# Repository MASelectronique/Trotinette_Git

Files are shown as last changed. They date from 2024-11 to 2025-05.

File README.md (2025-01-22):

Repos pour le système d'affichage de la trottinette électrique, projet étudiant du Cégep de Sherbrooke.

Code: Contient le code pour le prototype du système d'affichage.
Schéma: Contient les schémas (bloc, électrique et PCB) du prototype et du projet final.
Documentation: Contient les fichiers pour OSEntreprendre.

Créateurs: -Marc-Antoine Sauvé
           -Lucas Lalumière Longpré

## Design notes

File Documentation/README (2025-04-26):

Dossier Osentreprendre
Contient : 	- Osentreprendre v.2
			- PowerPoint du projet
 
Dossier PCB
Contient :	- Logo utilisé sur les PCB
			- Plan de test des PCB

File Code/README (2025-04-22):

Dossier principale (Code)

Contient : 	Fichier Controleur_client : Contient le code pour envoyer le JSON à partir du PCB de contrôle
		Fichier Developpement : Contient tous les anciens code utilisé l'ors du développement du projet
		Fichier EEZ_Studio : contient le projet du GUI de l'affichage
		Fichier Interface_V.1 : Projet à jour de l'affichage avec les librairies et le fichier main
		Fichier Interface_V.2 : Projet à jour de l'affichage et développement de l'intégration du JSON 
		Fichier Template_startip : C'Est un template pour partir un projet de zéro avec les lignes nécessaire pour que EEZ Studio, TFT, l'écran ainsi que le touch fonctionne			 
Language: C++
Environnement: Arduino avec board manager de ESP32 par Espressif Systems 2.0.14 (une version supérieur ne fonctionnera pas)
Plateforme: Arduino IDE 2.3.6

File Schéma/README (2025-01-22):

Dossier contenant le schéma pour le prototype et la version finale du système d'affichage.
Contient les schémas bloc, schémas électriques et PCB.

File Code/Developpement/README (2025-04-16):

Dossier secondaire (Developpement)

Contient : 	Fichier Accelerometre = Code pour le prototype du système d'affichage
		Fichier Affichage_retour_en_arriere (Plus utilisé) = Projet non commenté de test
		Fichier Affichage_test (Plus utilisé) = Développement du système d'affichage
		Fichier Affichage_touch_ui : Un test unitaire testant l'affichage, le touch de l'écran et le UI généré par EEZ studio. Inclus aussi toutes les libraires
		Fichier Telemetrie : Code de développement du module de télémétrie
		Fichier Touch_calibration = Code pour générer les données nécessaire à la calibration de l'écran
			
Language: C++
Environnement: Arduino avec board manager de ESP32 par Espressif Systems 2.0.14 (une version supérieur ne fonctionnera pas)
Plateforme: Arduino IDE 2.3.6

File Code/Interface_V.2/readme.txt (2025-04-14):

Dossier secondaire(Interface_V.2)

Contient : 	Fichier Affichage_V.2 : main pour faire afficher à l'écran avec des valeur aléatoire (en train d'intégrer le décodage du JSON)
		Fichier Libraries_backup : contient toute les libraries à jour pour faire fonctionner le projet

Language: C++
Environnement: Arduino avec board manager de ESP32 par Espressif Systems 2.0.14 (une version supérieur ne fonctionnera pas)
Plateforme: Arduino IDE 2.3.6

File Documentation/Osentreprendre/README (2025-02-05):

Dossier contenant tous les fichiers pour le concours OSEntreprendre.
Contient : 	- Texte explicatif
		- PowerPoint du projet
		- PowerPoint du présentoire

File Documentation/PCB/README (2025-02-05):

Dossier PCB
Contient :	- Logo utilisé sur les PCB
		- Plan de test des PCB

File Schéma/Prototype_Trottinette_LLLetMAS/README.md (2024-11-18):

Schéma électrique du prototype de l'affichage.
Concepteur: Lucas Lalumière Longpré

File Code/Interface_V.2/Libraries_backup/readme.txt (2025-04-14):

Dossier secondaire(Libraries_backup)

Contient : 		Fichier ArduinoJson : Librarie permettant le décodage d'un JSON 
			Fichier EspSoftwareSerial : Librarie permettant d'avoir un moniteur série en utilisant des GPIO différents de ceux proposé par l'ESP32
			Fichier ICM42670P : Librairie permettant la communication avec l'accéléromètre
			Fichier LVGL: Librarie avec la bonne configuration
			Fichier TFT_eSPI: Librarie avec la bonne configuration
			Fichier ui : interface généré de eez studio
			Fichier lv_conf.h : configuration de la livrairies de LVGL

Language: C++
Environnement: Arduino avec board manager de ESP32 par Espressif Systems 2.0.14 (une version supérieur ne fonctionnera pas)
Plateforme: Arduino IDE 2.3.6

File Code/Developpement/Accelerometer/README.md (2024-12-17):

Créateurs: 
  -Lucas Lalumière Longpré
  -Marc-Antoine Sauvé
Code pour le prototype du système d'affichage utilisé dans le projet de trottinette électrique. 
Calcule le roulis et le tangage d'un accéléromètre et l'affiche à un écran tactile. On peux aussi
tester la fonctionnalité tactile de l'écran. La DEL du MCU s'allume lorsque le roulis ou le tangage
est à plus de 30 degré (Trottinette sur le côté).

Librairies à installer:
  -TFT_eSPI (https://github.com/Bodmer/TFT_eSPI)

Plateforme: Platformio
Framework: Arduino
Langue: C++
Matériel:
  -MCU: ESP32-C3 DevkitC-02
  -Accel: MPU-6050
  -Écran: ILI9341

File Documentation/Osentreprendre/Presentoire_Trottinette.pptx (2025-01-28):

## Tableau de bord d'une trottinette électrique

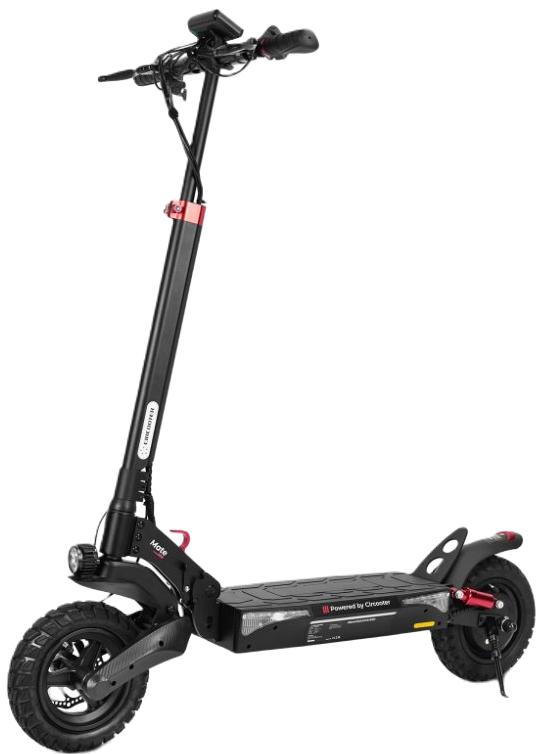
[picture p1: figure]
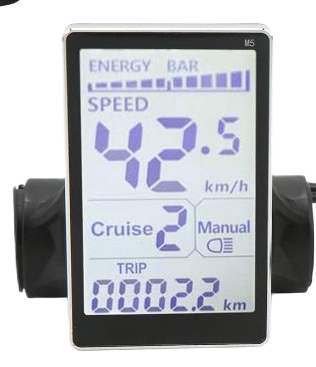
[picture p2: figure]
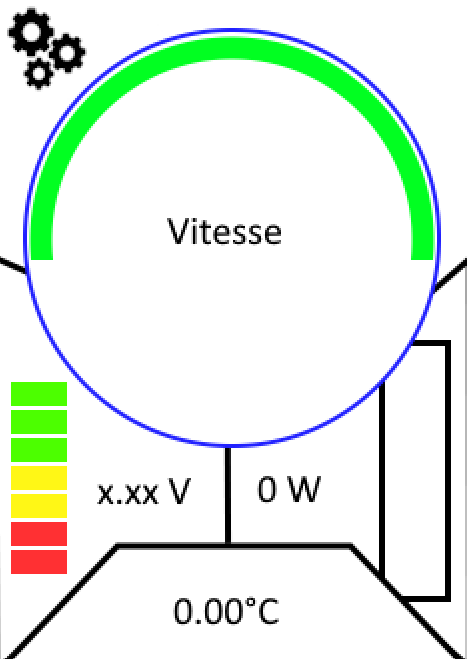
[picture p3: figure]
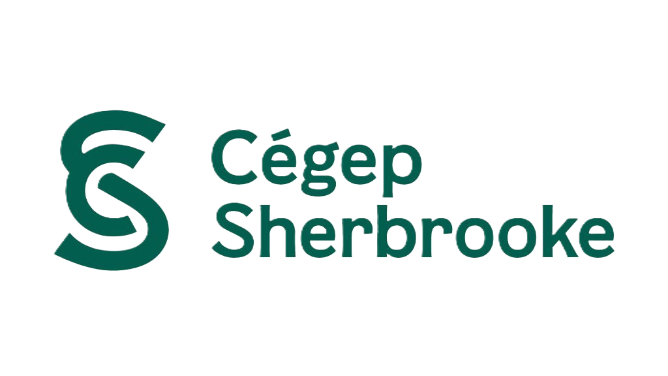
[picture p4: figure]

Tableau de bord

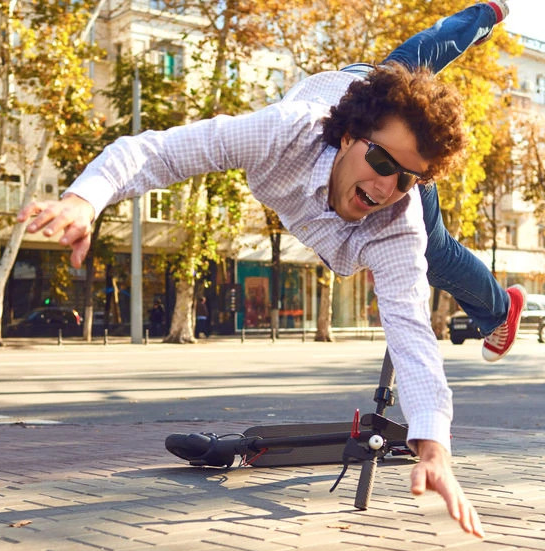
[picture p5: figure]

Détection de chute

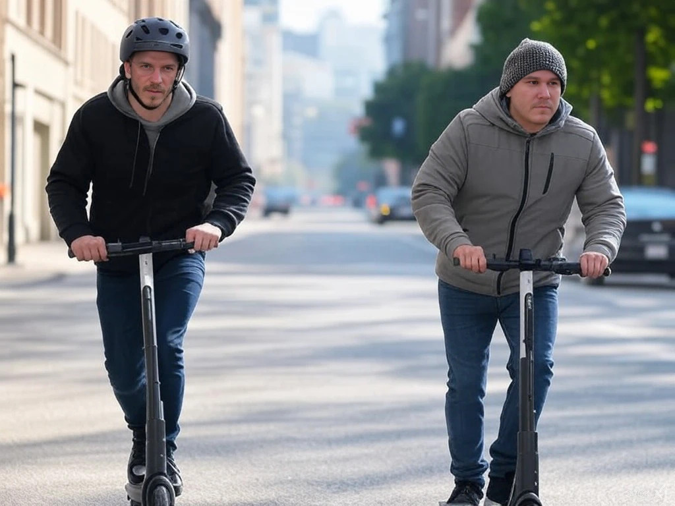
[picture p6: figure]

Marc-Antoine Sauvé et
Lucas Lalumière Longpré

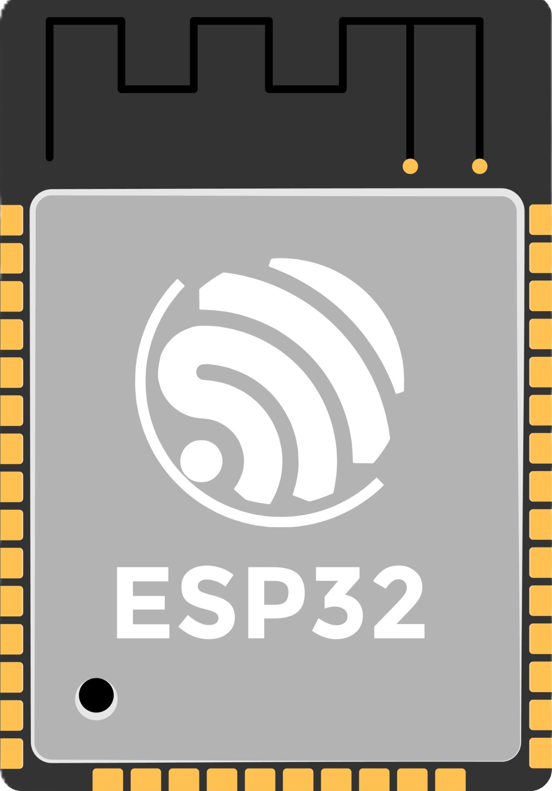
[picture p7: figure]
Vittascience — ESP32

Microcontrôleur

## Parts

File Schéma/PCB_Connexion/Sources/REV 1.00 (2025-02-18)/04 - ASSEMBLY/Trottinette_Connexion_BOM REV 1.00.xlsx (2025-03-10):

Bill of Material
Board | Trotinette_Connexion |  | Concepteur Principal |  | Marc-Antoine Sauvé |  |  | 1
Cours | 247-67P-SH PROJET DE FIN D'ÉTUDES |  | Date du projet |  | 22 janvier 2025 |  |  | 00
Département | Technologies du génie électrique |  | Date de génération du BOM |  | 2025-02-18
Révision | 1.00 |  | Heure de génération du BOM |  | 10:06
Nombre de PCB | 1 |  | Variant |  | None
Item Number | Designator | Layer | Description | Comment | Package / Case | Supplier 1 | Supplier Part Number 1 | Quantity | Quantity Total | Note
 | C1 | Top | General Purpose Ceramic Capacitor, 0603, 100nF, 20%, X7R, 15%, 10V | 0603ZC104MAT2A |  |  |  | 1 | 1
 | C2, C4 | Top | CAP CER 10UF 10V X5R 0603 | 10 µF | 0603 (1608 Metric) | DigiKey | 490-12311-1-ND | 2 | 2
 | C3, C5 | Top | CAP ALUM 100UF 20% 10V SMD | 100 µF | Radial, Can - SMD | DigiKey | 1189-2392-1-ND | 2 | 2
 | J1 | Bottom |  | 685119136923 |  |  |  | 1 | 1
 | Q1 | Bottom | MOSFET P-CHA 60V 720MW SOT23 | DMP6350S-7 |  |  |  | 1 | 1
 | R1 | Top | RESA-AS 0603 0R JUMPER 100MW | 0 Ohms | 0603 (1608 Metric) | DigiKey | CR0603AJ/-000EASCT-ND | 1 | 1
 | R2 | Bottom | 30Ohms | ERJ3EKF30R0V |  |  |  | 1 | 1
 | R3 | Top | RES 180 OHM 1% 1/8W 0603 | 180 Ohms | 0603 (1608 Metric) | DigiKey | RNCP0603FTD180RCT-ND | 1 | 1
 | R4 | Top | RES SMD 300 OHM 1% 1/10W 0603 | 300 Ohms | 0603 (1608 Metric) | DigiKey | 541-300HCT-ND | 1 | 1
 | R5 | Bottom | RES 10K OHM 0.1% 1/16W 0603 | 10 kOhms | 0603 (1608 Metric) | DigiKey | RNCS0603BKE10K0CT-ND | 1 | 1
 | S1 | Top | 3.2" 240x320 TFT LCD ILI9341 | ILI9341 |  |  |  | 1 | 1
 | U1 | Top | 800mA Low-Dropout Linear Regulator, 4-pin SOT-223 | LM1117MPX-ADJ |  |  |  | 1 | 1
Commentaires ou instruction spécialies

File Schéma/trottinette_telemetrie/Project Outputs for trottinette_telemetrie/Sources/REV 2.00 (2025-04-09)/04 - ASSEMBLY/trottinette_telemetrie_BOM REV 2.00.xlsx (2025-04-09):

Bill of Material
Board | Trottinette - Module de télémétrie |  | Concepteur Principal |  | Lucas Lalumière Longpré |  |  | 2
Cours | 247-67P-SH PROJET DE FIN D'ÉTUDES |  | Date du projet |  | 08-04-2025 |  |  | 00
Département | Technologies du génie électrique |  | Date de génération du BOM |  | 4/9/2025
Révision | 2.00 |  | Heure de génération du BOM |  | 9:57 AM
Nombre de PCB | 1 |  | Variant |  | None
Item Number | Designator | Layer | Description | Comment | Package / Case | Supplier 1 | Supplier Part Number 1 | Quantity | Quantity Total | Note
 | C1, C13 | Top | CAP ALUM 100UF 20% 10V SMD | 100 µF | Radial, Can - SMD | DigiKey | 1189-2392-1-ND | 2 | 2
 | C2, C3, C8, C9, C14 | Top, Bottom | CAP CER 10UF 10V X5R 0603 | 10 µF | 0603 (1608 Metric) | DigiKey | 490-12311-1-ND | 5 | 5
 | C4, C5, C10, C11 | Bottom, Top | General Purpose Ceramic Capacitor, 0603, 100nF, 20%, X7R, 15%, 10V | 0603ZC104MAT2A |  |  |  | 4 | 4
 | C6 | Top | CAP CER 0603 10NF 16V X7R 10% | 10000 pF | 603 | DigiKey | 399-17880-1-ND | 1 | 1
 | C7 | Top | CAP CER 2.2UF 16V Y5V 0603 | 2.2 µF | 603 | DigiKey | 311-3416-1-ND | 1 | 1
 | C12 | Top | CAP CER 10000PF 100V X7R 0603 | 10000 pF | 0603 (1608 Metric) | DigiKey | 311-3100-1-ND | 1 | 1
 | D1 | Top | TVS DIODE 5.25V 17V SOT666 | USBLC6-2P6 |  |  |  | 1 | 1
 | D2 | Top | DIODE SCHOTTKY 15V 1A DO214BA | LSM115JE3/TR13 |  |  |  | 1 | 1
 | D3 | Top | LED GREEN 0603 SMD | Green | 0603 (1608 Metric) | DigiKey | 350-4373-1-ND | 1 | 1
 | D4 | Top | LED YELLOW 0603 SMD | Yellow | 0603 (1608 Metric) | DigiKey | 350-4349-1-ND | 1 | 1
 | J1 | Top | CONN RCP USB2.0 TYP C 24P SMD RA | DX07S016JA1R1500 |  |  |  | 1 | 1
 | J2, MT1, R12, R14, R15, R16 | Top |  | 685119136923, ICM-42670-P, ERJ3EKF30R0V |  |  |  | 6 | 6
 | P1 | Bottom | WR-PHD Pin Header, THT, Vertical, pitch 2.54mm, 1 Row, 6P | 61300611121 |  |  |  | 1 | 1
 | P2 | Bottom | WR-PHD Pin Header, THT, Vertical, pitch 2.54mm, 1 Row, 8P | 61300811121 |  |  |  | 1 | 1
 | P3 | Top | WR-PHD Pin Header, THT, Vertical, pitch 2.54mm, 1 Row, 2P | 61300211121 |  |  |  | 1 | 1
 | R1 | Top | RES 150 OHM 1% 1/10W 0603 | 150 Ohms | 0603 (1608 Metric) | DigiKey | RMCF0603FT150RCT-ND | 1 | 1
 | R2 | Top | RES 250 OHM 5% 1/8W 0603 | 250 Ohms | 0603 (1608 Metric) | DigiKey | 716-1168-1-ND | 1 | 1
 | R3, R11 | Bottom | RES 5.1K OHM 1% 1/10W 0603 | 5.1 k | 603 | DigiKey | RMCF0603FT5K10CT-ND | 2 | 2
 | R4, R5, R6, R10 | Bottom, Top | RES 10K OHM 0.1% 1/16W 0603 | 10k | 0603 (1608 Metric) | DigiKey | RNCS0603BKE10K0CT-ND | 4 | 4
 | R7, R8 | Top | RES 124K OHM 1% 1/10W 0603 | 124 k | 0603 (1608 Metric) | DigiKey | RMCF0603FT124KCT-ND | 2 | 2
 | R9 | Bottom | RES 63.4K OHM 1% 1/10W 0603 | 63.4 k | 0603 (1608 Metric) | DigiKey | RMCF0603FT63K4CT-ND | 1 | 1
 | R13 | Top | 0603 26 AMP JUMPER | 0 Ohms | 0603 (1608 Metric) | DigiKey | JR0603X26ECT-ND | 1 | 1
 | R17, R18 | Top | RES SMD 1K OHM 0.1% 1/16W 0603 | 1 kOhms | 0603 (1608 Metric) | DigiKey | A119887CT-ND | 2 | 2
 | TP1 | Top | TPO - PC TEST POINT MINI - SMD | TPO_SMD_5019 |  |  |  | 1 | 1
 | U1 | Top | 800mA Low-Dropout Linear Regulator, 4-pin SOT-223 | LM1117MPX-ADJ |  |  |  | 1 | 1
 | U2 | Top | Bluetooth, WiFi 802.11b/g/n, Bluetooth v5.0 Transceiver Module 2.4GHz Antenna Not Included, U.FL Surface Mount | ESP32-S3-WROOM-1U-N16R8 |  |  |  | 1 | 1
 | U3 | Top | Low Quiescent Current, Programmable-Delay Supervisory Circuit, 1 Supply Monitored, -40 to 125 degC, 6-pin SOT-23 (DBV), Green (RoHS & no Sb/Br) | TPS3808G01DBVR |  |  |  | 1 | 1
Commentaires ou instruction spécialies

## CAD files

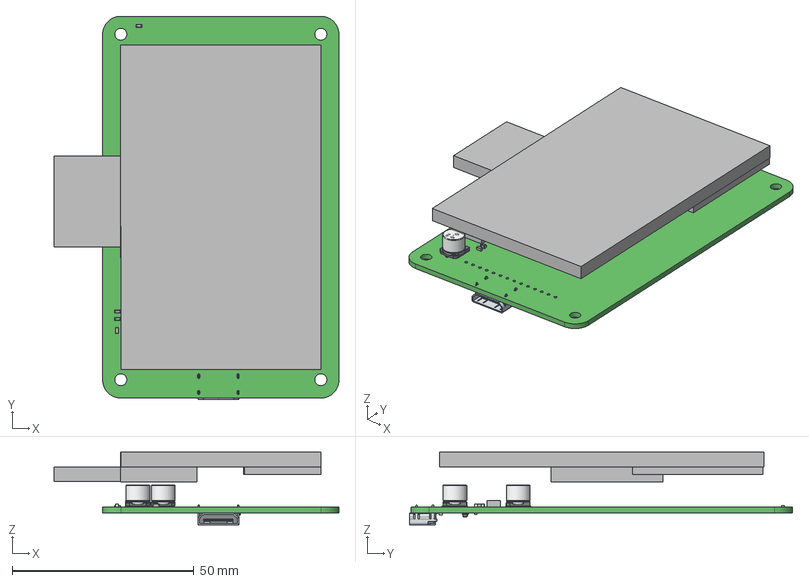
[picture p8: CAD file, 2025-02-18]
Schéma/PCB_Connexion/Sources/REV 1.00 (2025-02-18)/05 - 3D MODEL/Trottinette_Connexion_PCB REV 1.00.step
78.4 x 105.4 x 20.0 mm
Extruded x 8
0603 resistor x 4
pins
part number & logo
CAP ALSMD - 6.6 x 6.6 x 6.1 x 2
0603 cap x 2
Terminals
AVX
685119136923_Housing
685119136923_Shielding
685119136923_Housing2
685119136923_Pin1 x 18
685119136923_Pin2

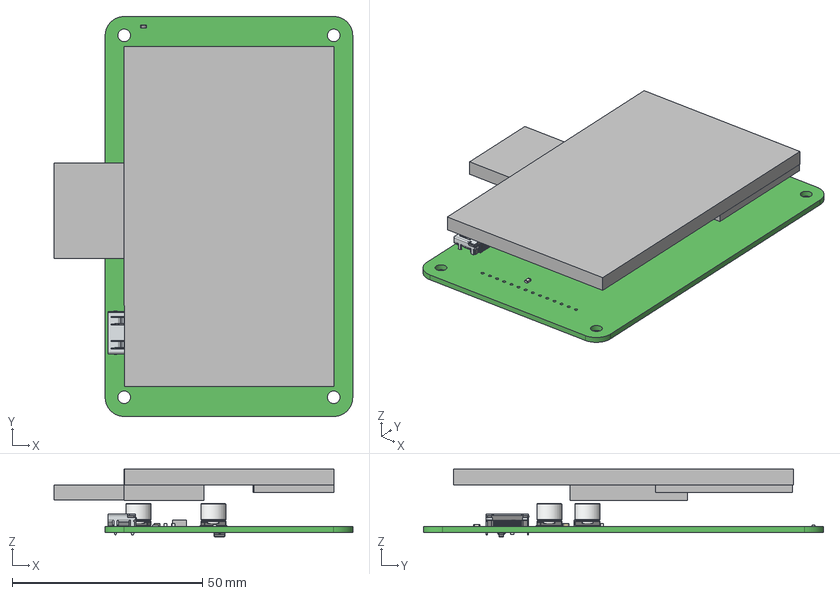
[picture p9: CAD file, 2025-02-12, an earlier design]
Schéma/PCB_Connexion/Sources/REV 1.00 (2025-02-11)/05 - 3D MODEL/Trottinette_Connexion_PCB REV 1.00.step
78.4 x 105.0 x 17.8 mm
0603 resistor x 4
pins
part number & logo
Extruded x 8
CAP ALSMD - 6.6 x 6.6 x 6.1 x 2
0603 cap x 2
Terminals
AVX
685119136923_Housing
685119136923_Shielding
685119136923_Housing2
685119136923_Pin1 x 18
685119136923_Pin2

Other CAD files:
Schéma/PCB_Connexion/Trottinette_Connexion_2L.step
Schéma/PCB_Connexion/Sources/REV 1.00 (2025-02-11)/05 - 3D MODEL/Trottinette_Connexion_PCB REV 1.00.x_t
Schéma/PCB_Connexion/Sources/REV 1.00 (2025-02-18)/05 - 3D MODEL/Trottinette_Connexion_PCB REV 1.00.x_t

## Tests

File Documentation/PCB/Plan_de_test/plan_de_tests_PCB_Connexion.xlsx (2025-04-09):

 | Plan de tests
Nom du PCB | Trottinette_Connexion | Préparé par | Marc-Antoine Sauvé
Cours | 247-67P-SH PROJET DE FIN D'ÉTUDES | Testeur | Lucas Lalumière Longpré
Département | Technologies du génie électrique | date | 27/2/2025
Révision | 1.00
Fonction | Test | Résultat | Commentaires
Régulateur | La tension d'entrée est à 5V | Réussi
 | La tension de sortie est à 3V3 | Réussi
Écran | Est-ce que la chip sur l'écran pour activé le touch est présente? | Réussi
 | Est-ce que l'écran s'insert bien dans les pin header femelle? | Réussi
 | Insérer l'écran sur le PCB de connexion, connecter le port mini-HDMI du PCB de connexion à celui du PCB de télémétrie. Brancher le port USB-C du PCB de télémétrie pour alimenter le tout. Mettre le programme <<Accelerometre>> du git dans le MCU à l'aide de plateforme.io. Est-ce que l'écran affiche les angles ?
 | En gardant le branchement mentionné plus haut ainsi que le code, est-ce que lorsqu'on touche l'écran, il est affiché à l'écran.
Alimentation | Il n'y a pas de court-circuit à l'alimentation | Réussi | 400 Ω entre GND et 3V3
Modifications / commentaires pour une deuxième version du PCB
1 | Cable HDMI ne s'insert pas comme il faut
2
3
4
5
6
7
8
9
10

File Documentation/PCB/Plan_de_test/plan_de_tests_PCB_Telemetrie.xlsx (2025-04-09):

 | Plan de tests
Nom du PCB | trottinette_telemetrie | Préparé par | Marc-Antoine Sauvé
Cours | Techniques de conception d'un prototype (247-425-SH) | Testeur
Département | Technologies du génie électrique | date
Révision | 1.00
Fonction | Test | Résultat | Commentaires
Pour cette section, brancher le PCB de télémétrie par USB-C, connecter le port mini-HDMI au PCB de connexion et programmer le MCU avec le programme du prototype (Git)
Regulateur 5V à 3V3 | La tension d'entrée est à 5V | Réussi | 4.79 V Mesuré
 | La tension de sortie est à 3V3 | Réussi | 3.32 V Mesuré
 | Le régulateur supporte un courant de sortie de 300mA (3.3V en sortie avec une resistance de 11ohm, 5Watt) | Réussi | 303 mA mesuré
Acceléromètre | Est ce qu'on peut lire les données de l'accélérateur | Réussi
I2C
Interruption | À l'aide d'un oscilloscope, est ce que les interruptions de l'accéléromètre deviennent active lorsque le PCB est sur le coter? | Réussi | Il y a un délai de 2 sec pour que l'angle soit détectée
Circuit de protection | Un court-circuit sur la sortie du régulateur ne court-circuite pas l'alimentation USB de 5V | Réussi
MOSFET / signal LED_Control | Est-ce qu'on peut fermer l'écran à l'aide du signal LED | Réussi
Pour cette section, déconnecter le cabe USB-C et le connecteur mini-HDMI.
Propriétés physique | Est-ce que les pin header s'insert facilement dans le PCB de contrôle de la trottinette? | Réussi
Redémarrage | Le bouton de reset du PCB de contrôle permet-il un bon redémarrage du MCU du PCB de télémétrie ? | Réussi
Court-circuit | Il n'y a pas de court-circuit entre 5V/VUSB et GND | Réussi | Environ 260 kΩ entre 5V et GND
Modifications / commentaires pour une deuxième version du PCB
1 | résistance de pull down sur GPIO46 pour boot mode
2 | DEL verte pour alimentation
3 | Déplacer CON_GPIO18 et CON_GPIO21 sur les pattes 10 et 11 du MCU
4 | Réduction de la longueur des traces USB
5 | Enlever la pull-up sur EN
6 | Changer pattes UART
7
8
9
10

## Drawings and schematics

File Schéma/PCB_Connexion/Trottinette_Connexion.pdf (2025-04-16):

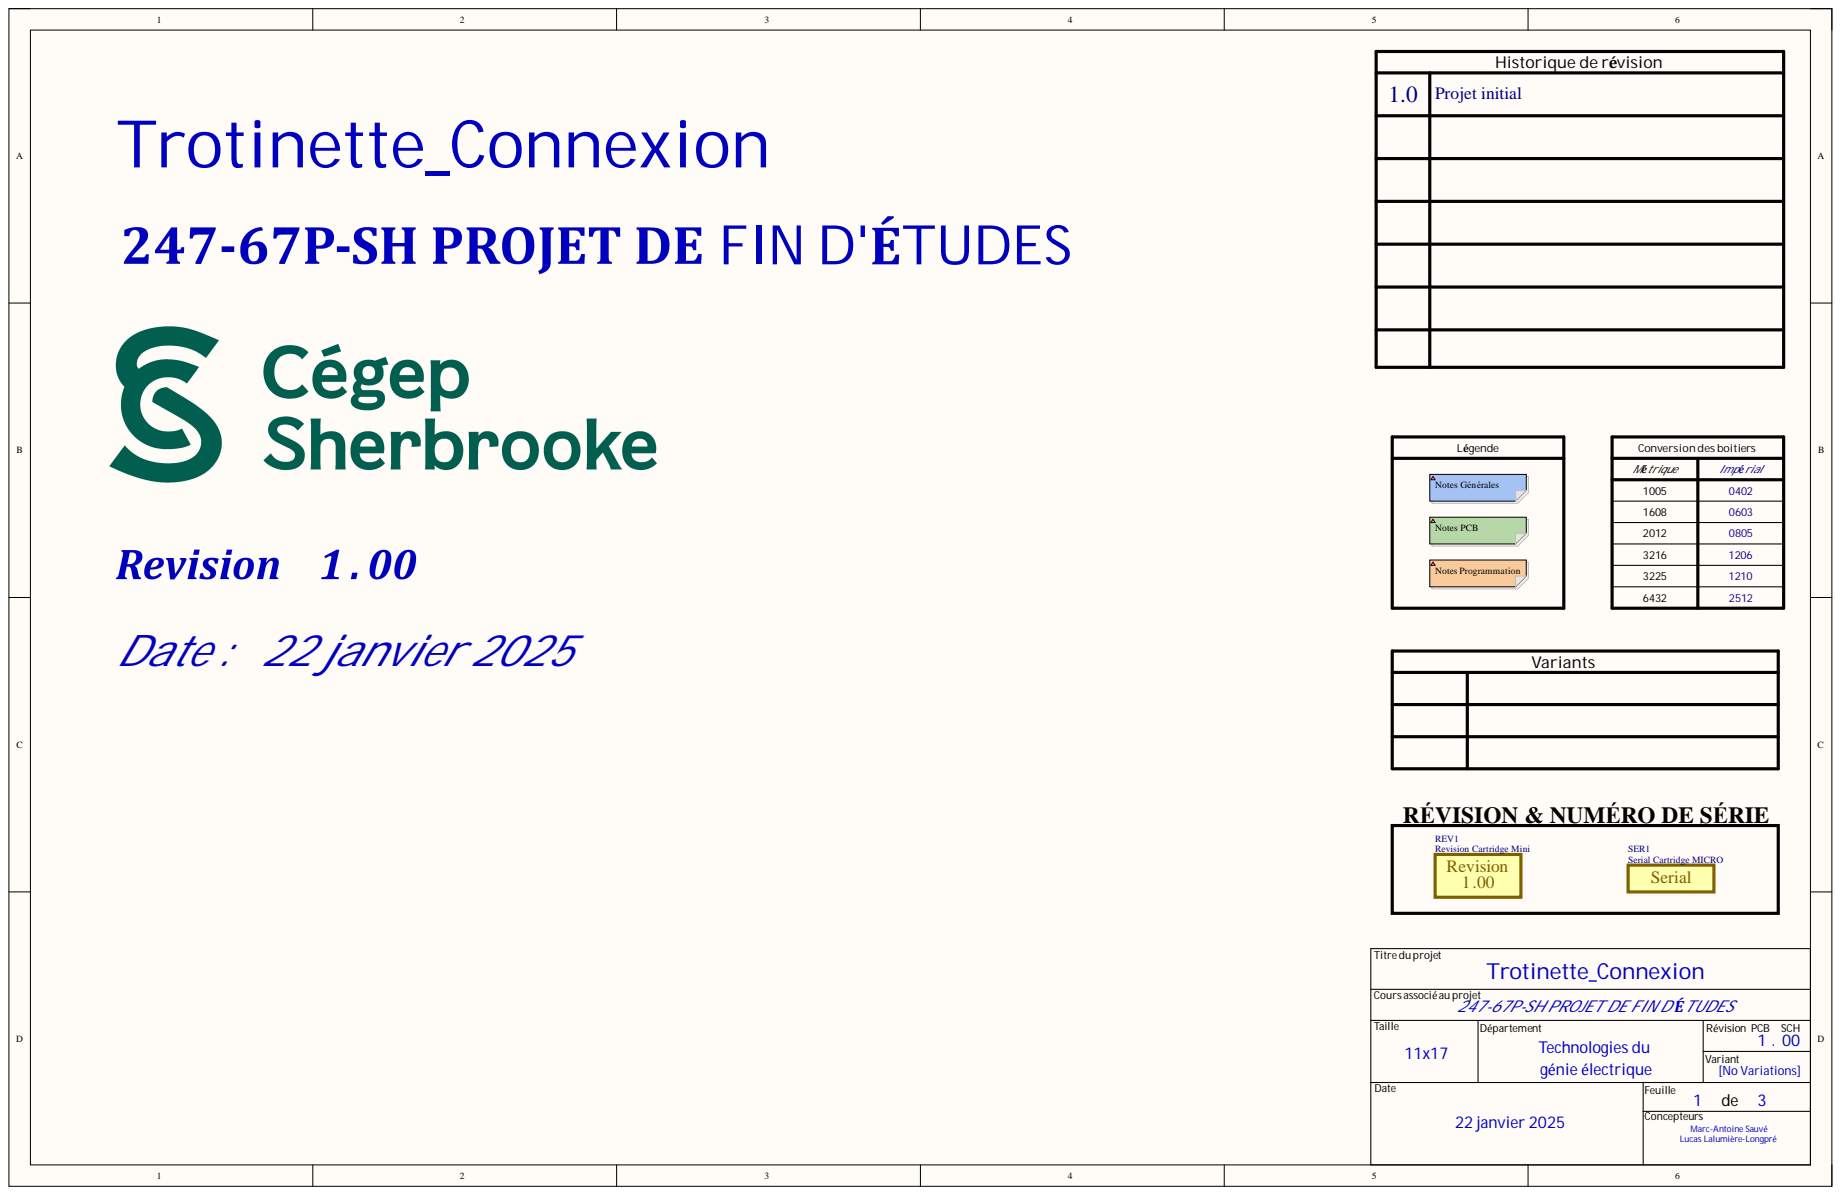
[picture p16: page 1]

-SH PROJET DE FIN D

Titr
rotinette_Connexion Cours associé au projet

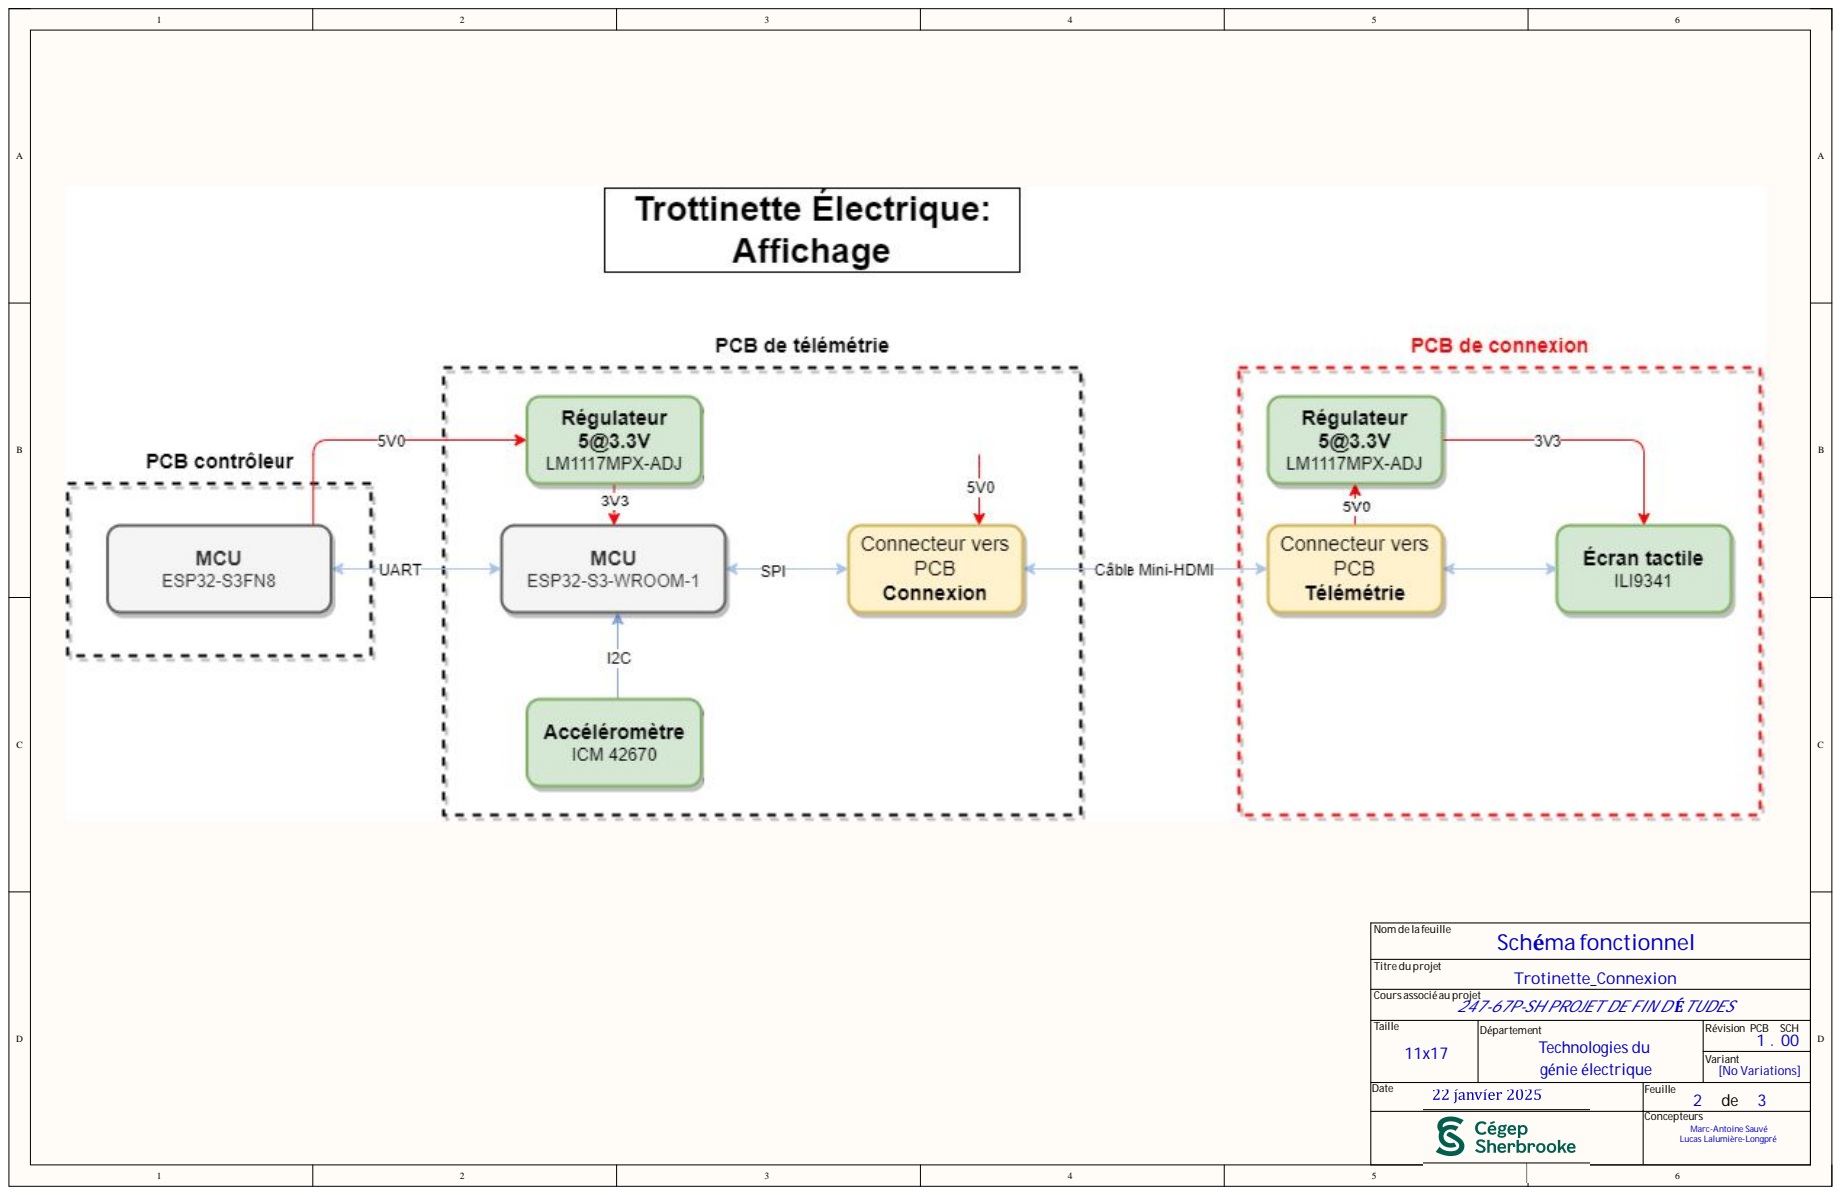
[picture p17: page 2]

Nom de la feuille

Titredu projet
Trotinette_Connexion Cours associé au projet

247-67P-SH PROJET DE FIN D'ÉTUDES

Date 22 janvier 2025 | Feuille 2 de Concepteurs 3

Marc-Antoine Sauvé Lucas Lalumière-Longpré

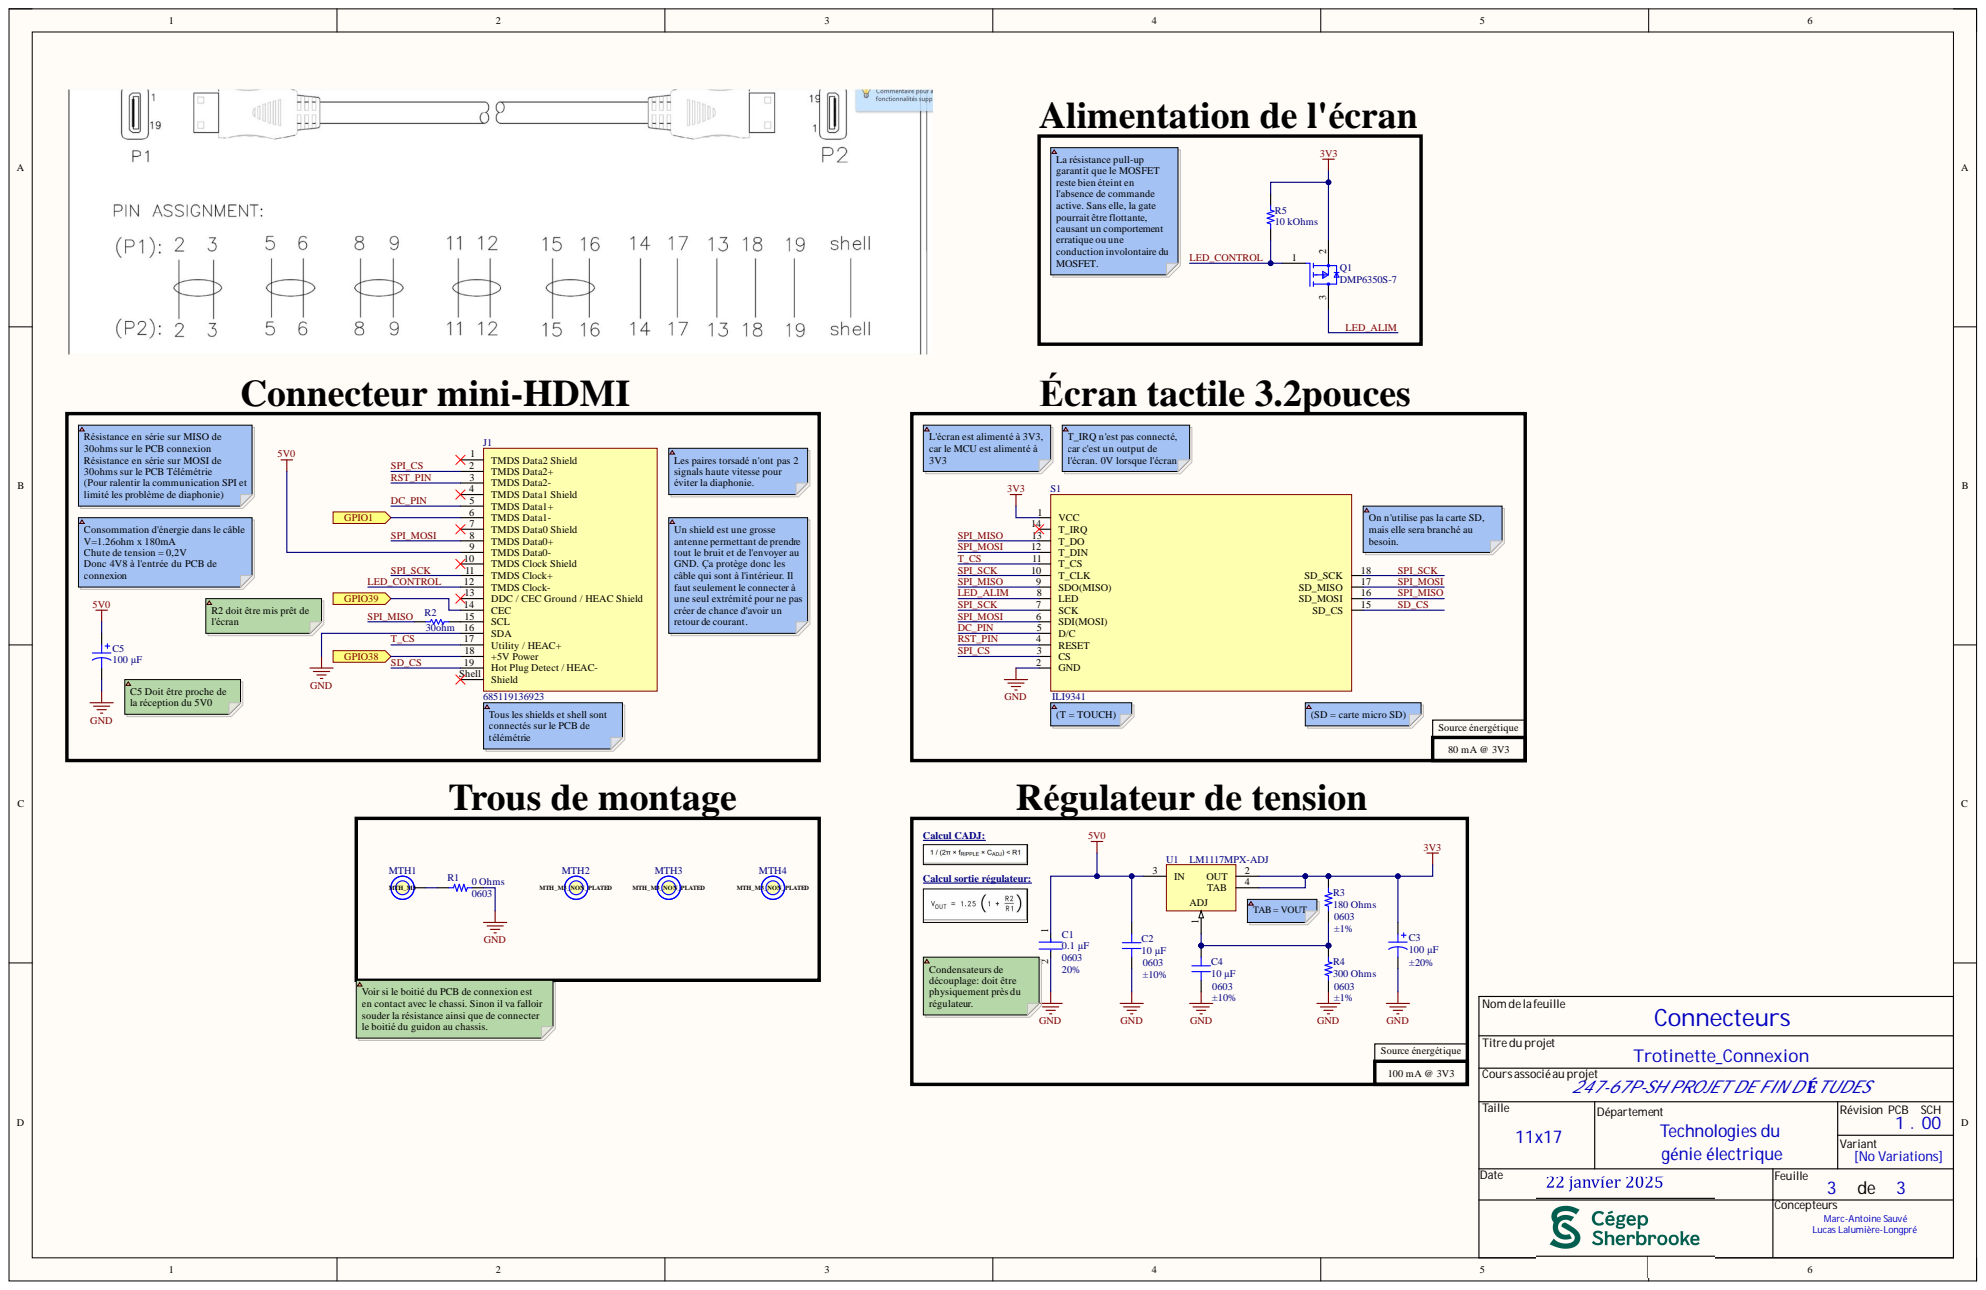
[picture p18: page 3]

Connecteur mini-HDMI Trous de montage

ésistance en
ms sur le PCB con
ms sur le PCB
tir la com

érie sur MISO de

mais elle sera branch
besoin

tilise pas la carte SD,

ten
t le bruit et de l'envoyer au
Ça prot
âble qui son
t seulemen
ne seul ext
retour de couran

ée du PCB de

éer de chance d'avoir

és sur le PCB de

Condensateurs de découplage: doit ê

Voir si le boit
en con
souder la
le boit

tact avec le chassi. Sinon il va falloir

é du PCB de con

ésistance ainsi que de con
é du guidon au chassis.

Date 22 janv ier 2025 | Feuil l e 3 de Concepteurs 3

Marc-A n toi n e Sa uv é Lu cas La l umi ère-Lon gp r é

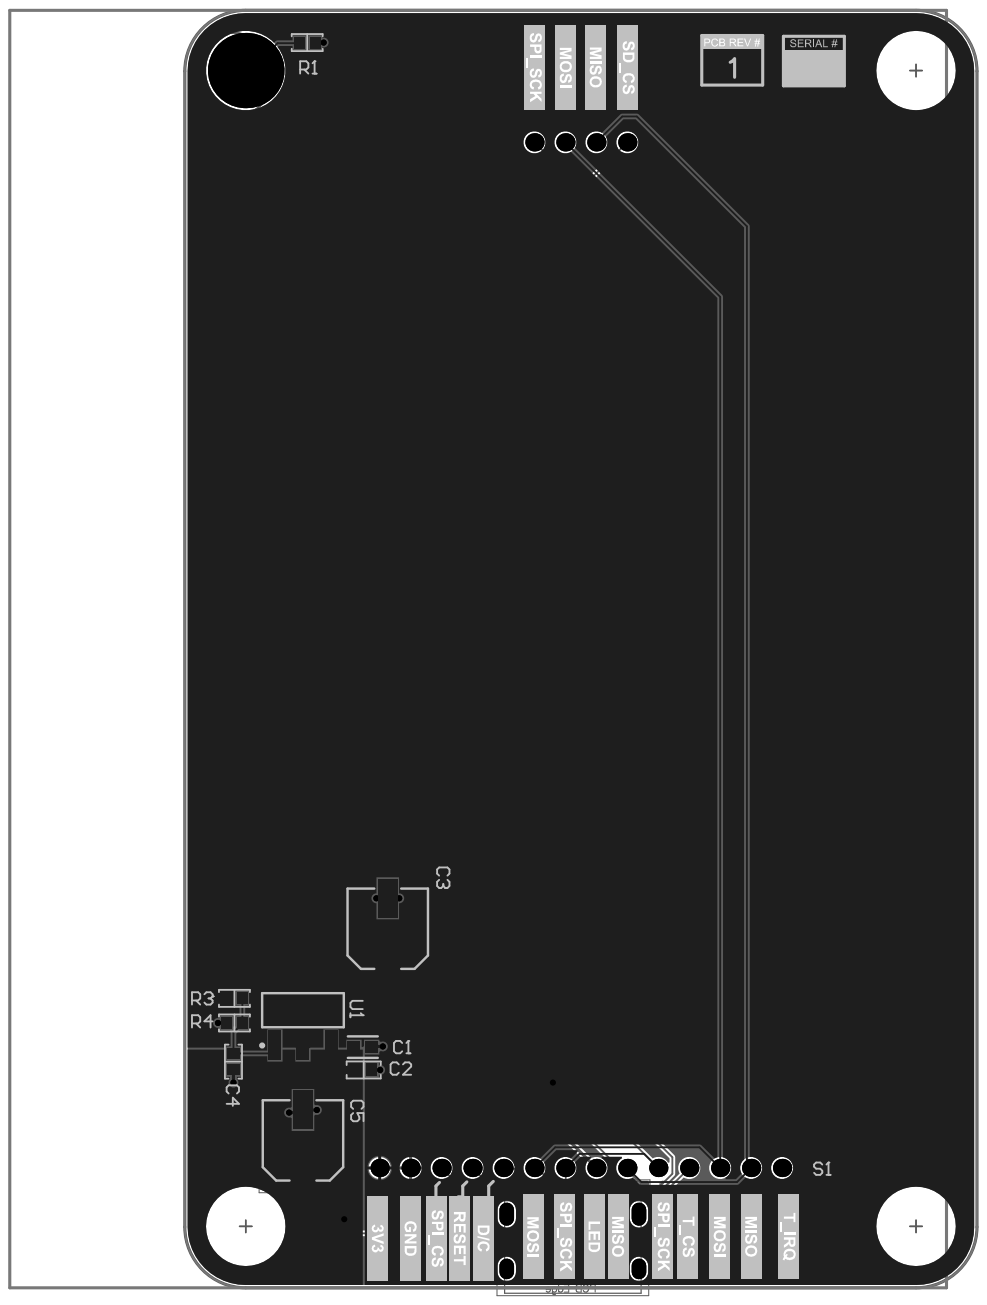
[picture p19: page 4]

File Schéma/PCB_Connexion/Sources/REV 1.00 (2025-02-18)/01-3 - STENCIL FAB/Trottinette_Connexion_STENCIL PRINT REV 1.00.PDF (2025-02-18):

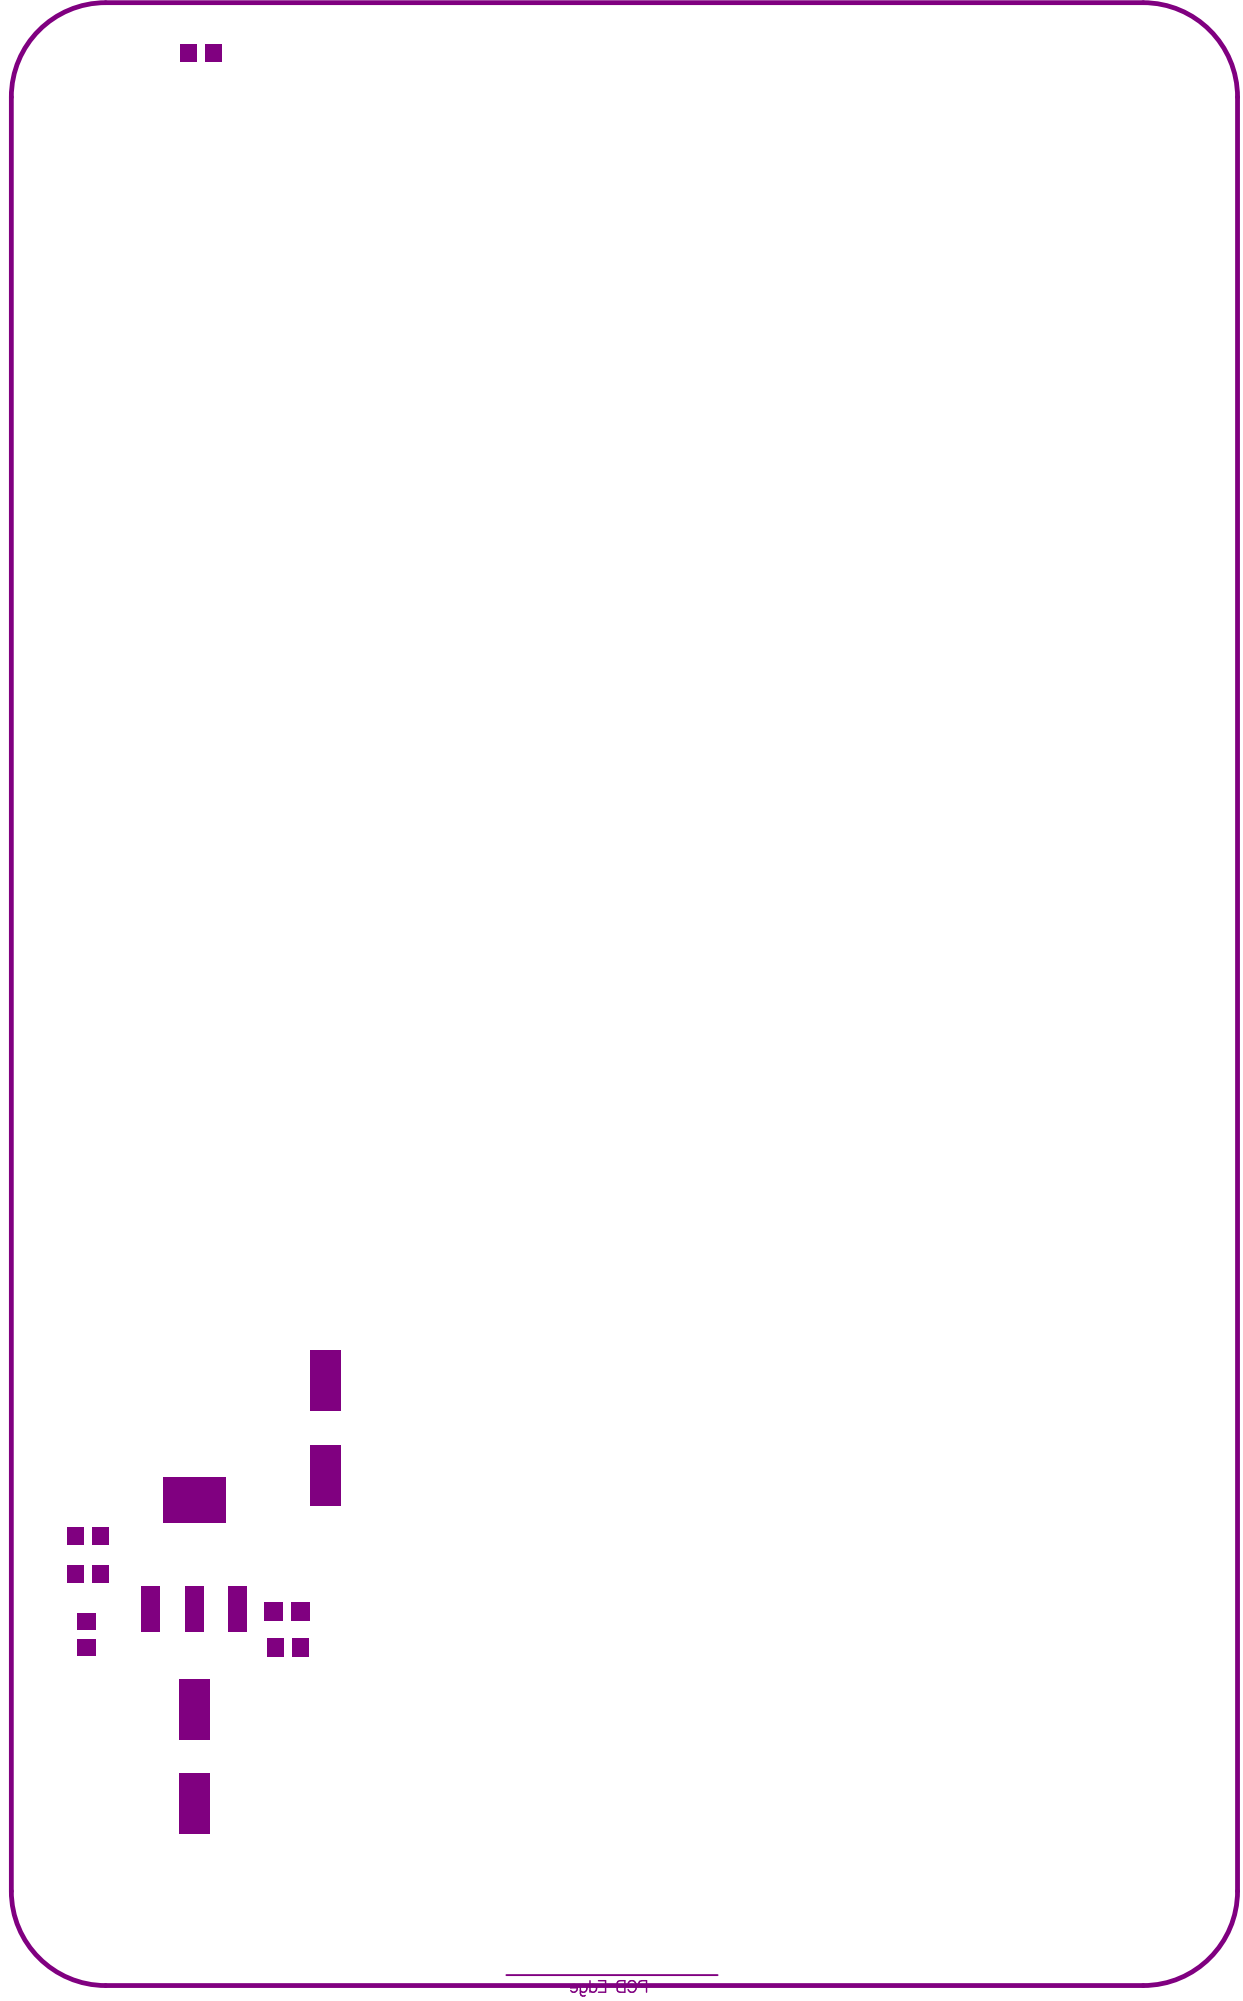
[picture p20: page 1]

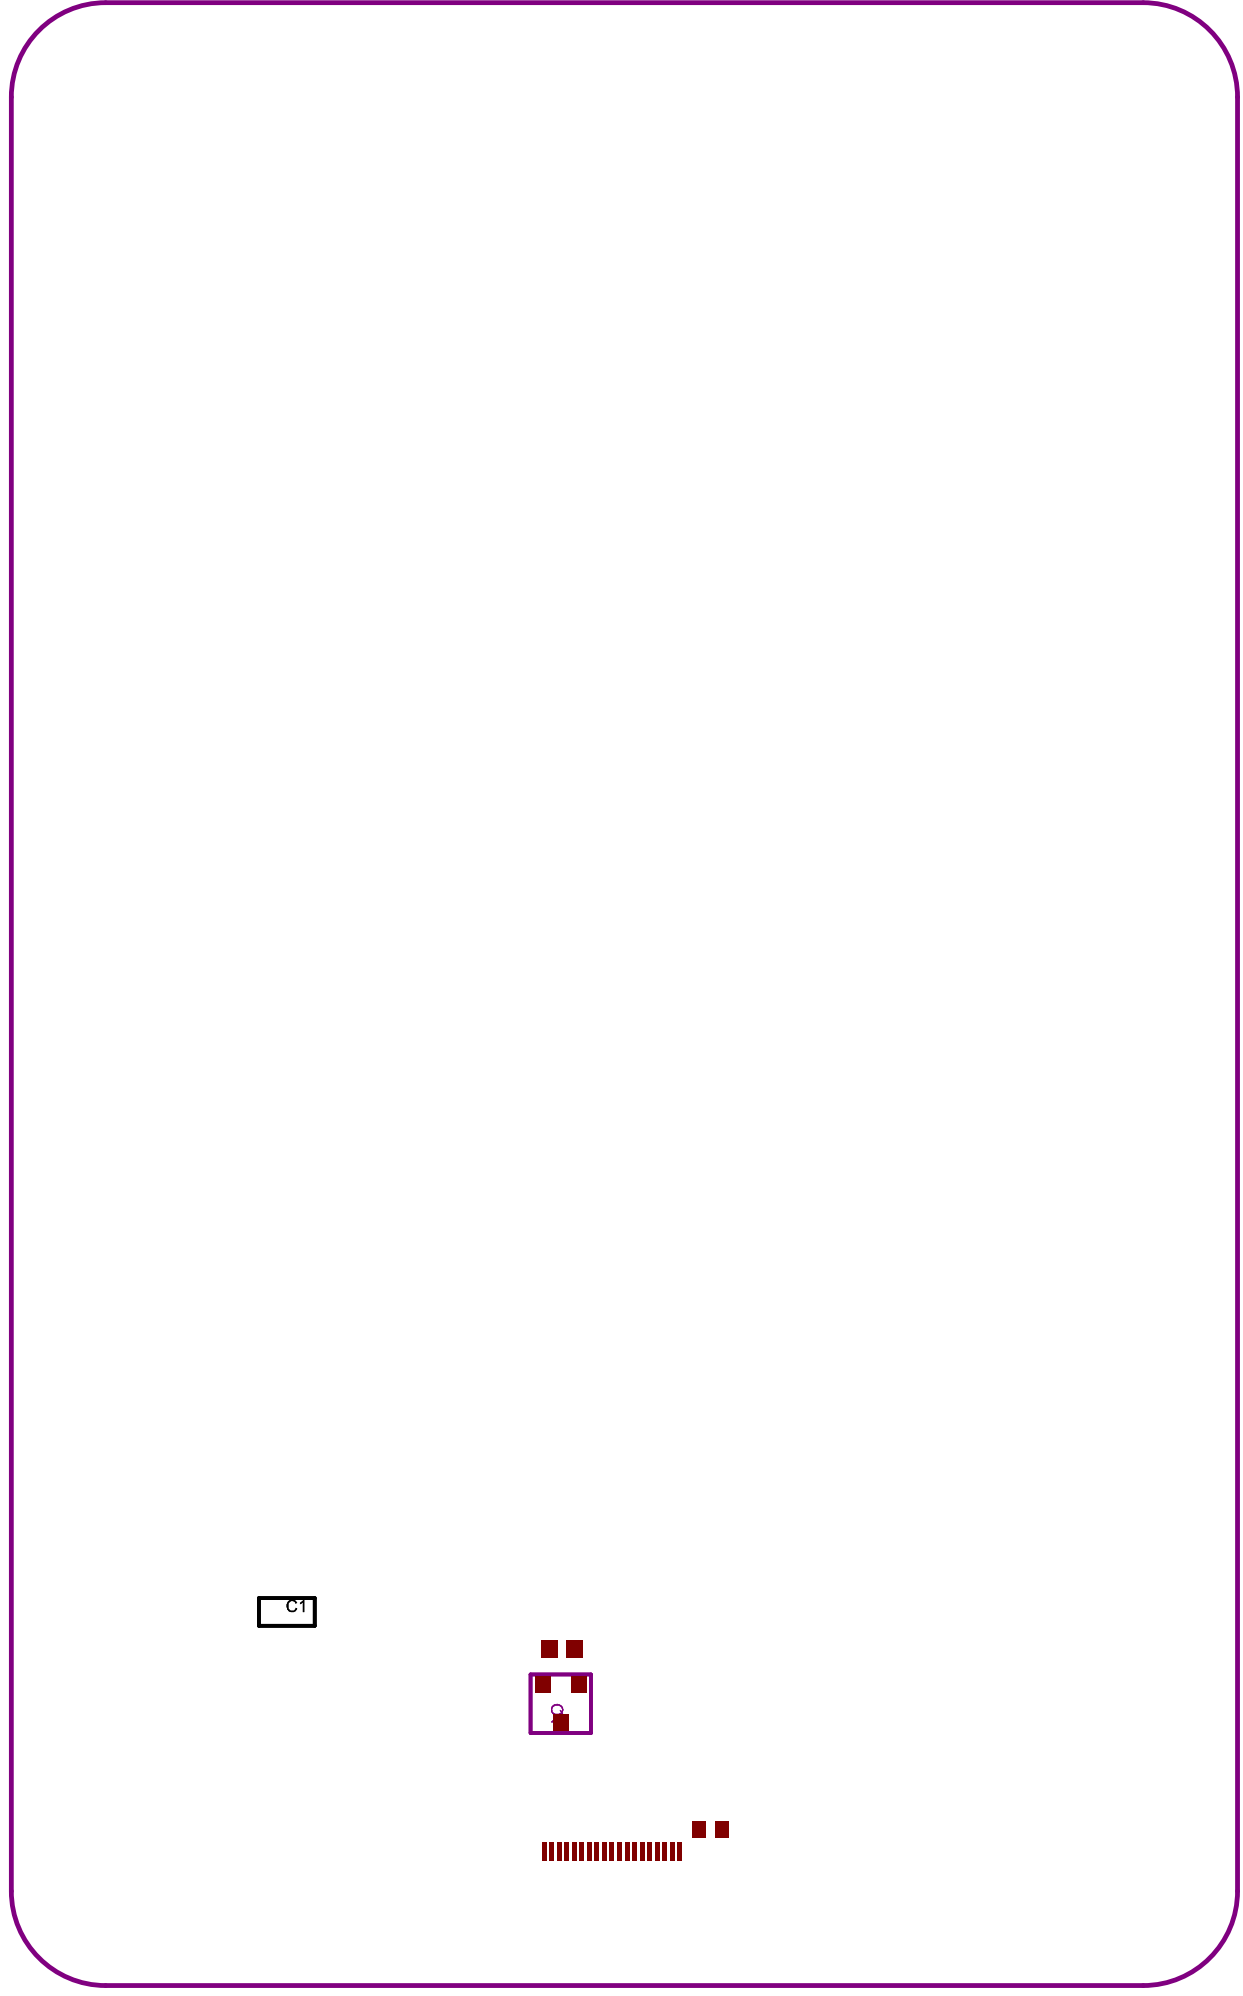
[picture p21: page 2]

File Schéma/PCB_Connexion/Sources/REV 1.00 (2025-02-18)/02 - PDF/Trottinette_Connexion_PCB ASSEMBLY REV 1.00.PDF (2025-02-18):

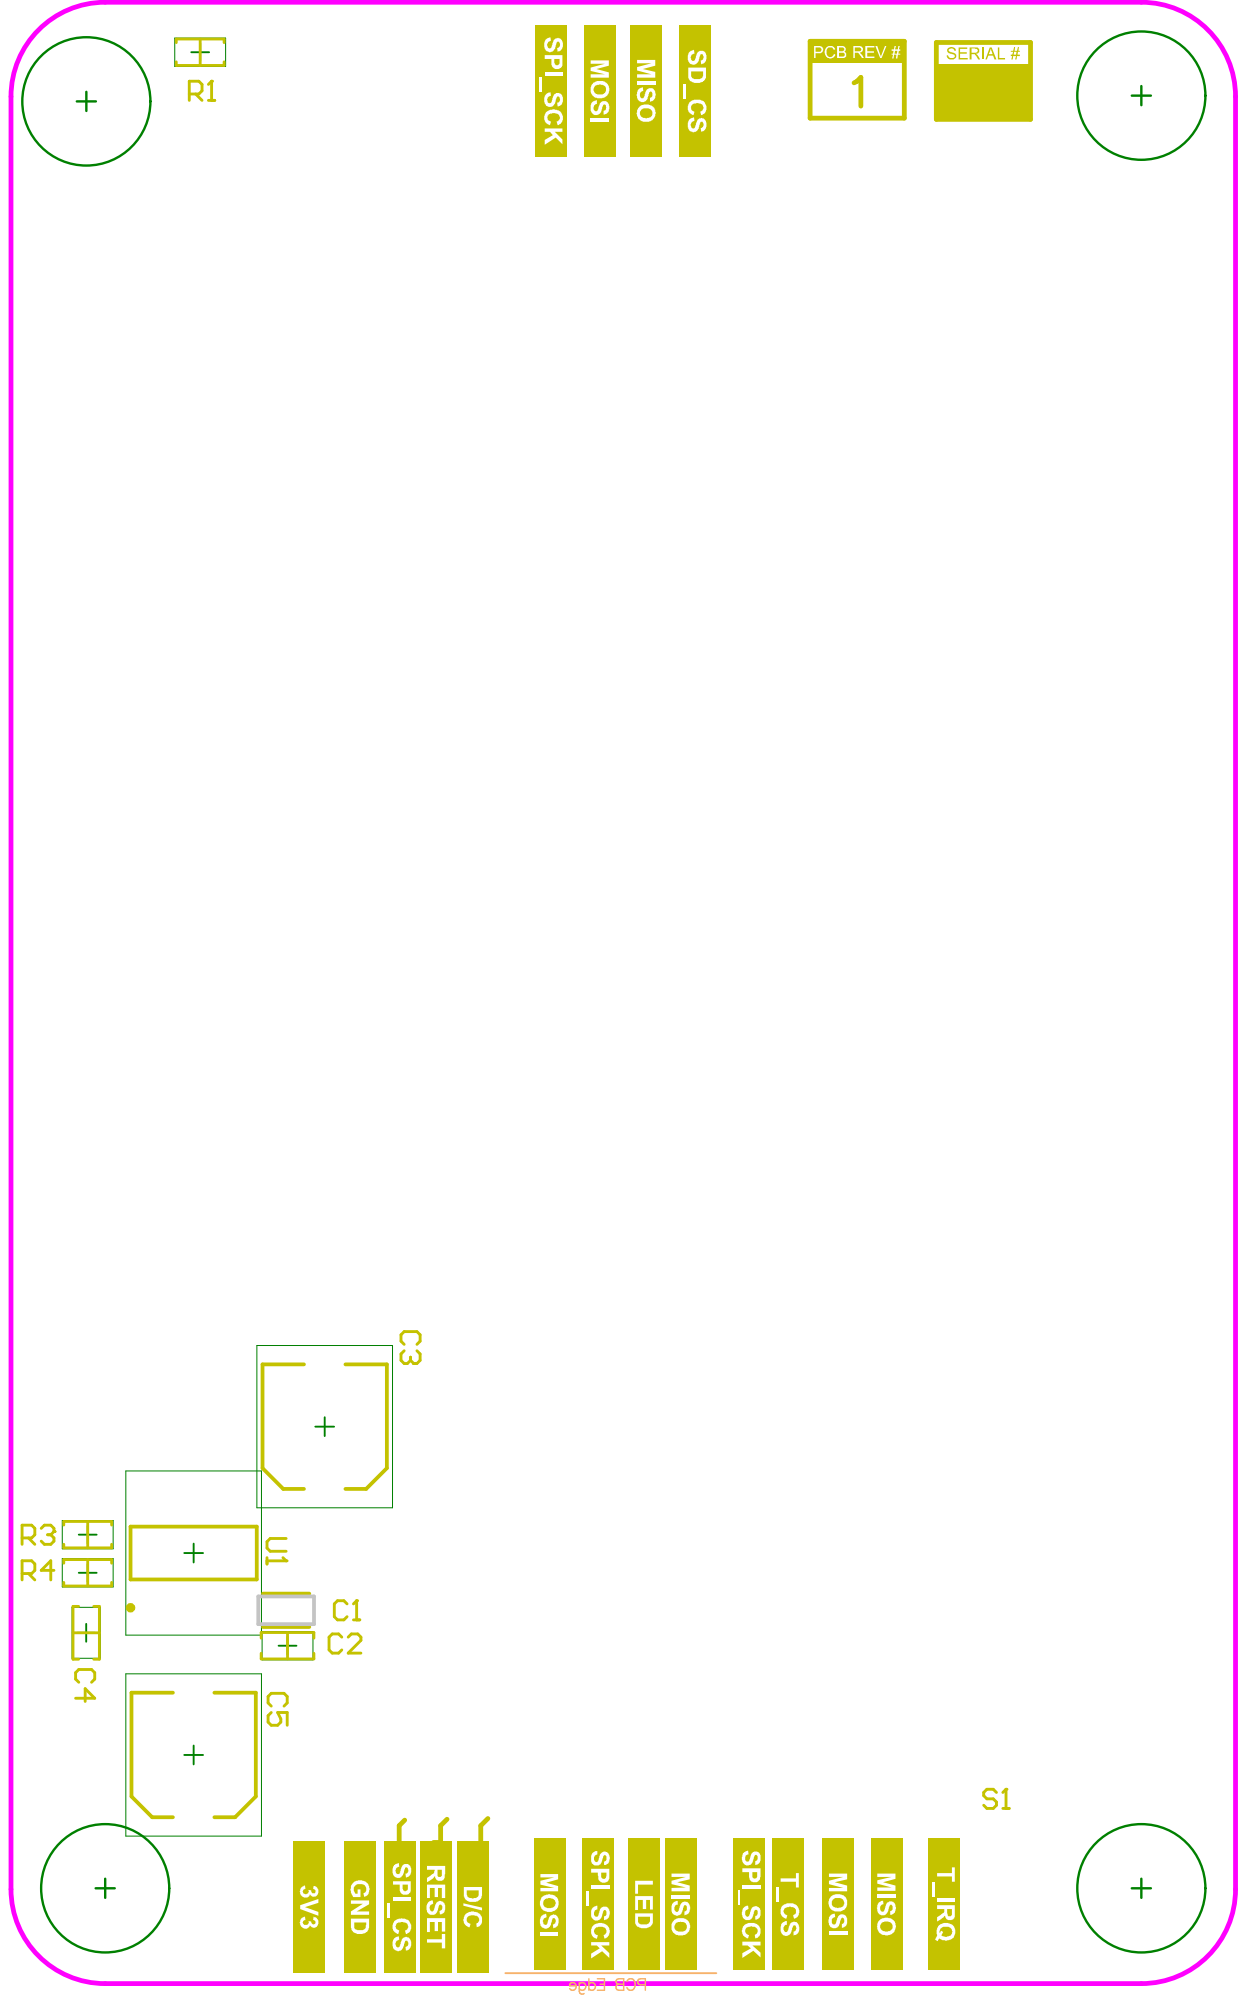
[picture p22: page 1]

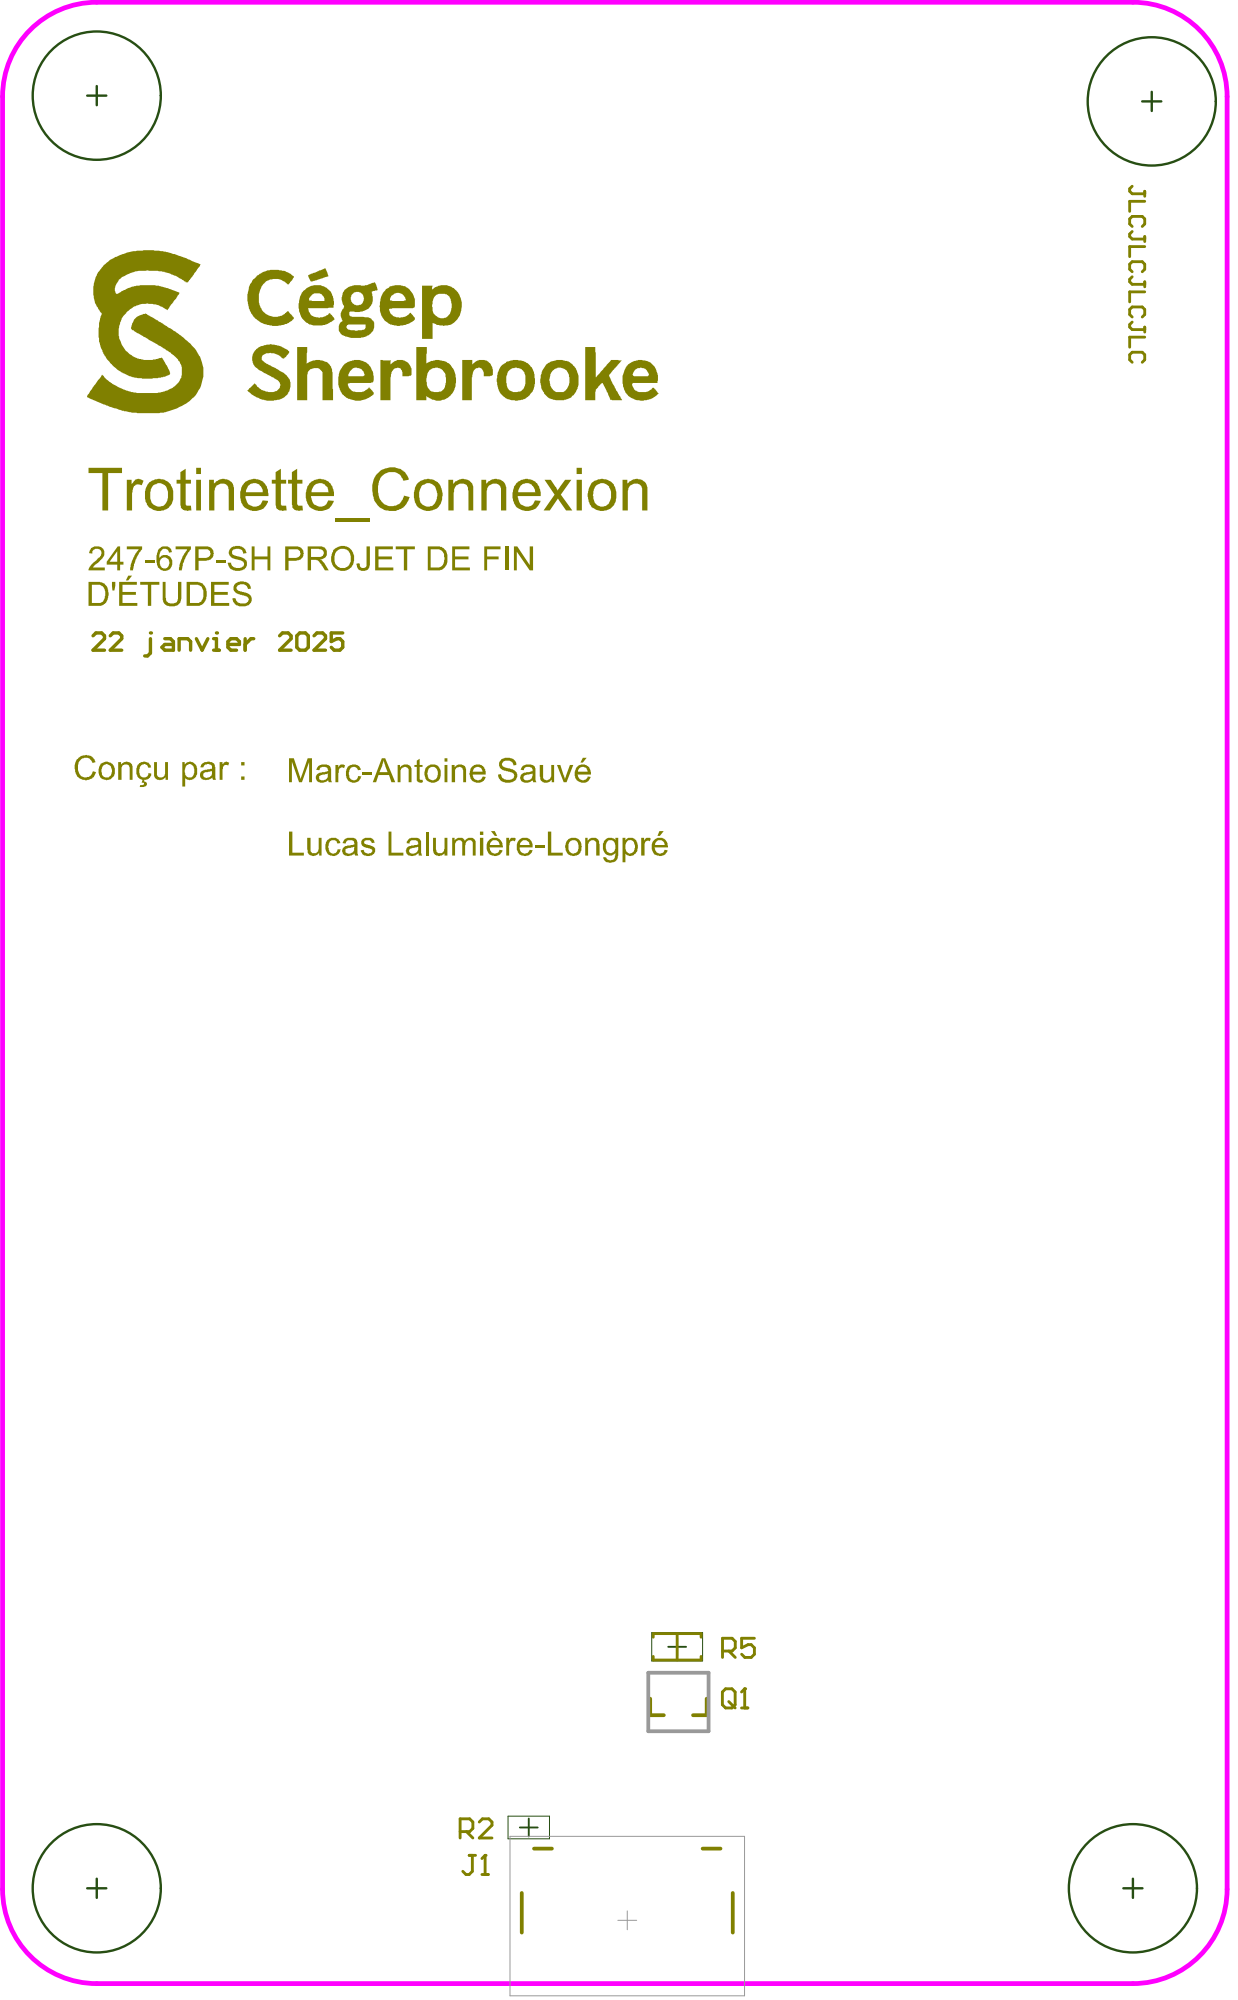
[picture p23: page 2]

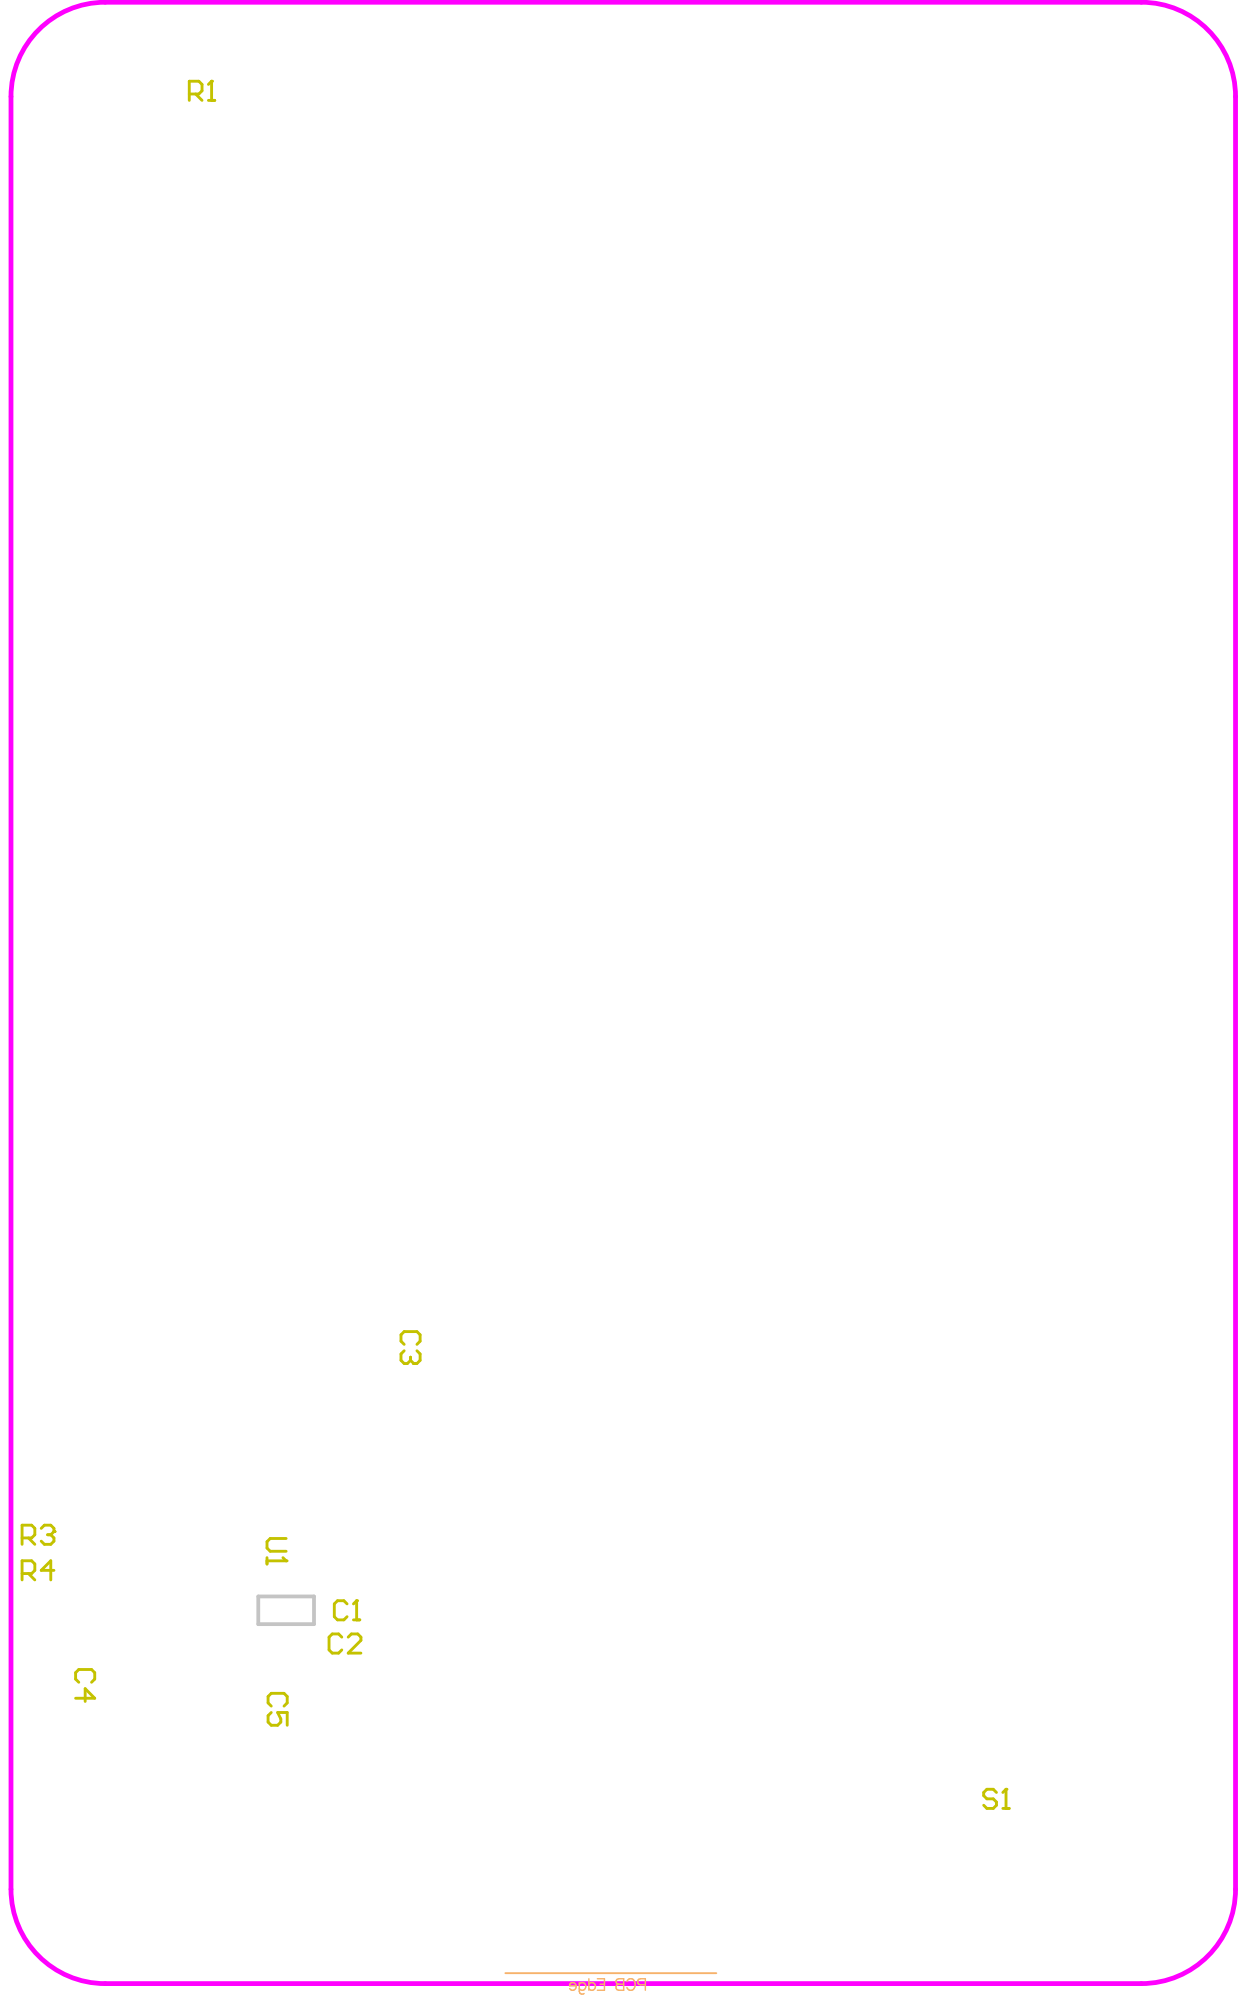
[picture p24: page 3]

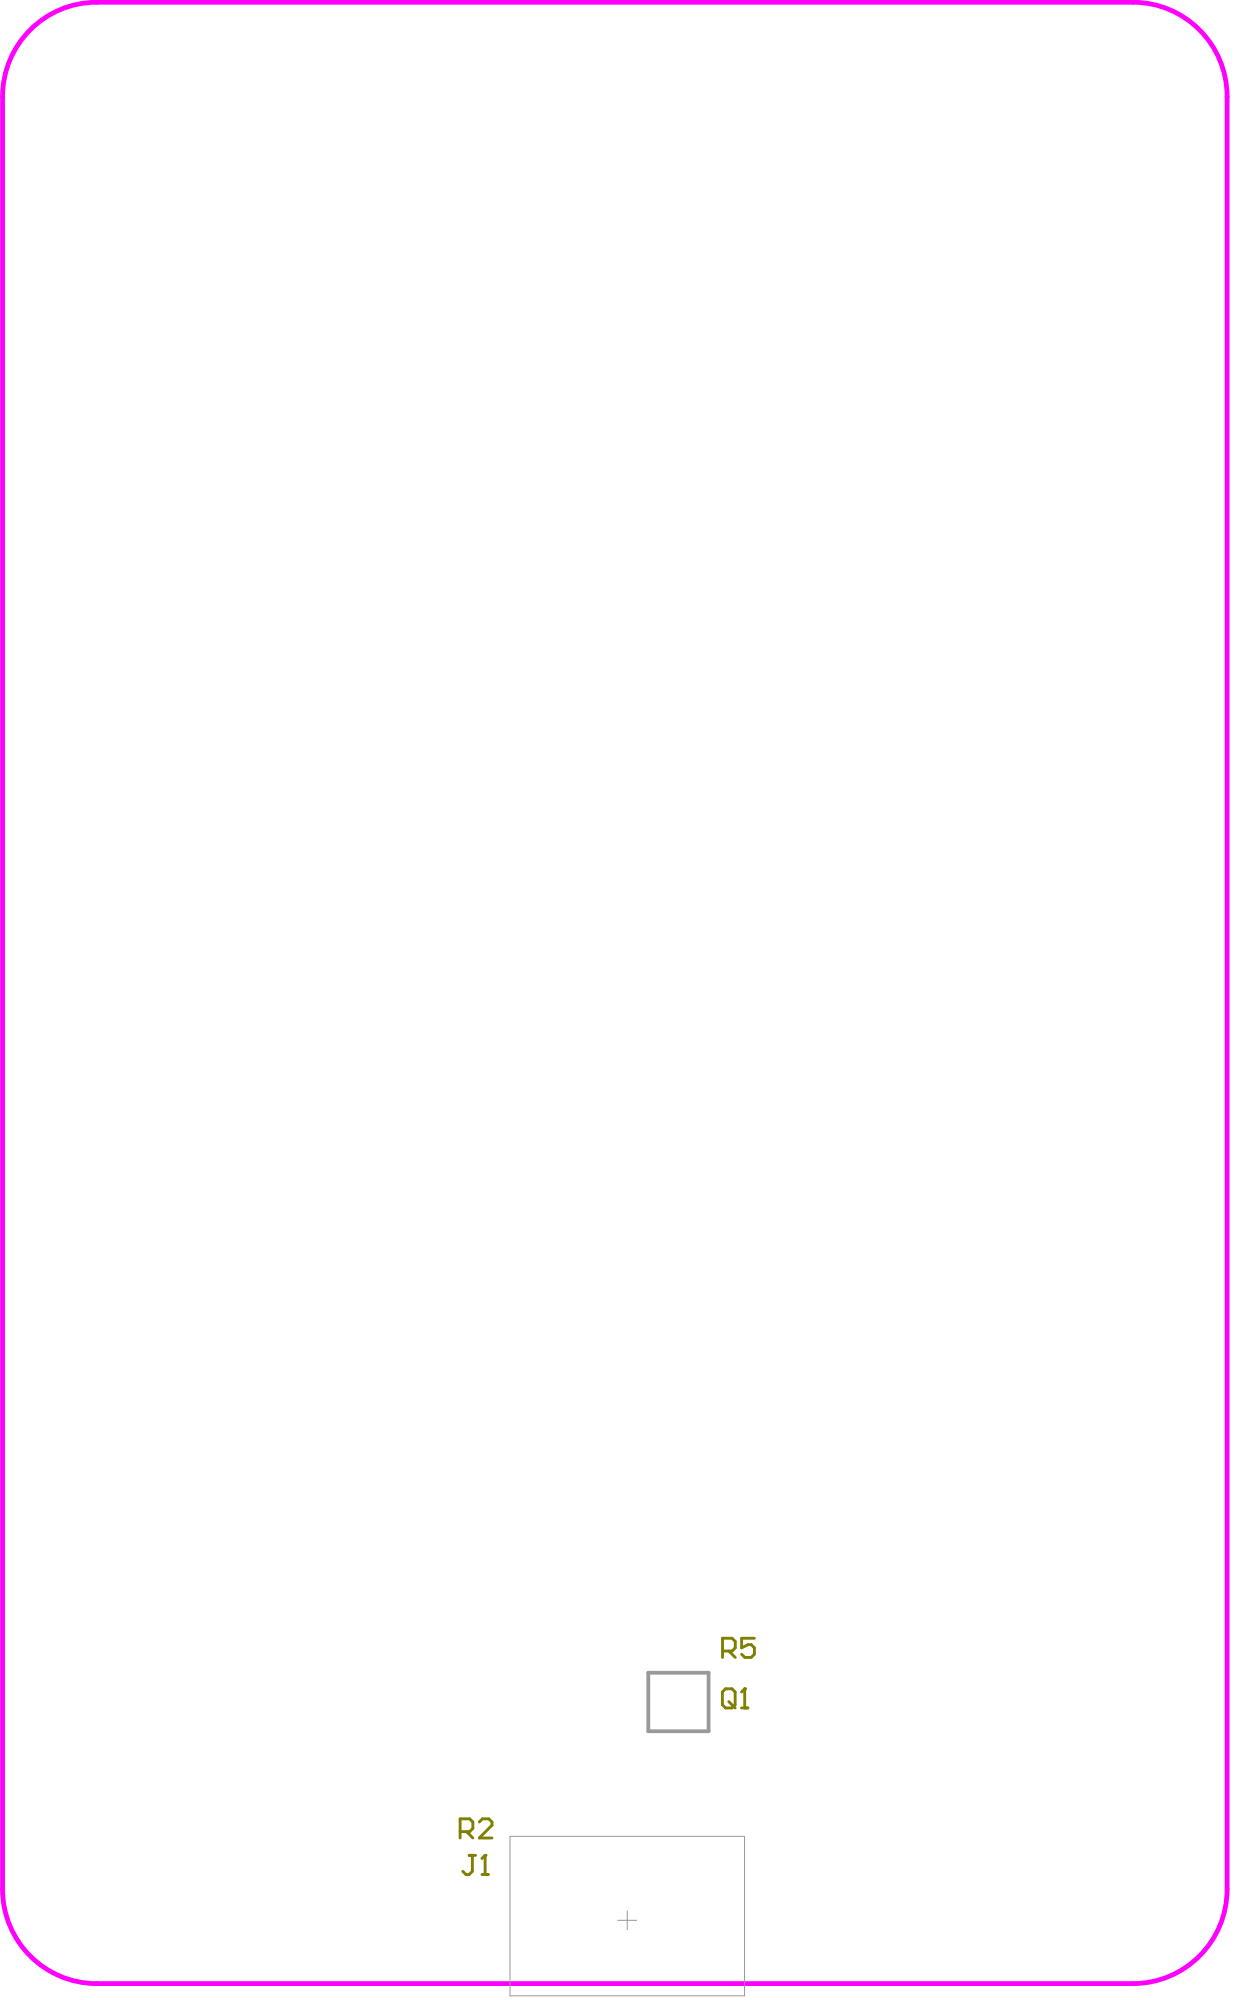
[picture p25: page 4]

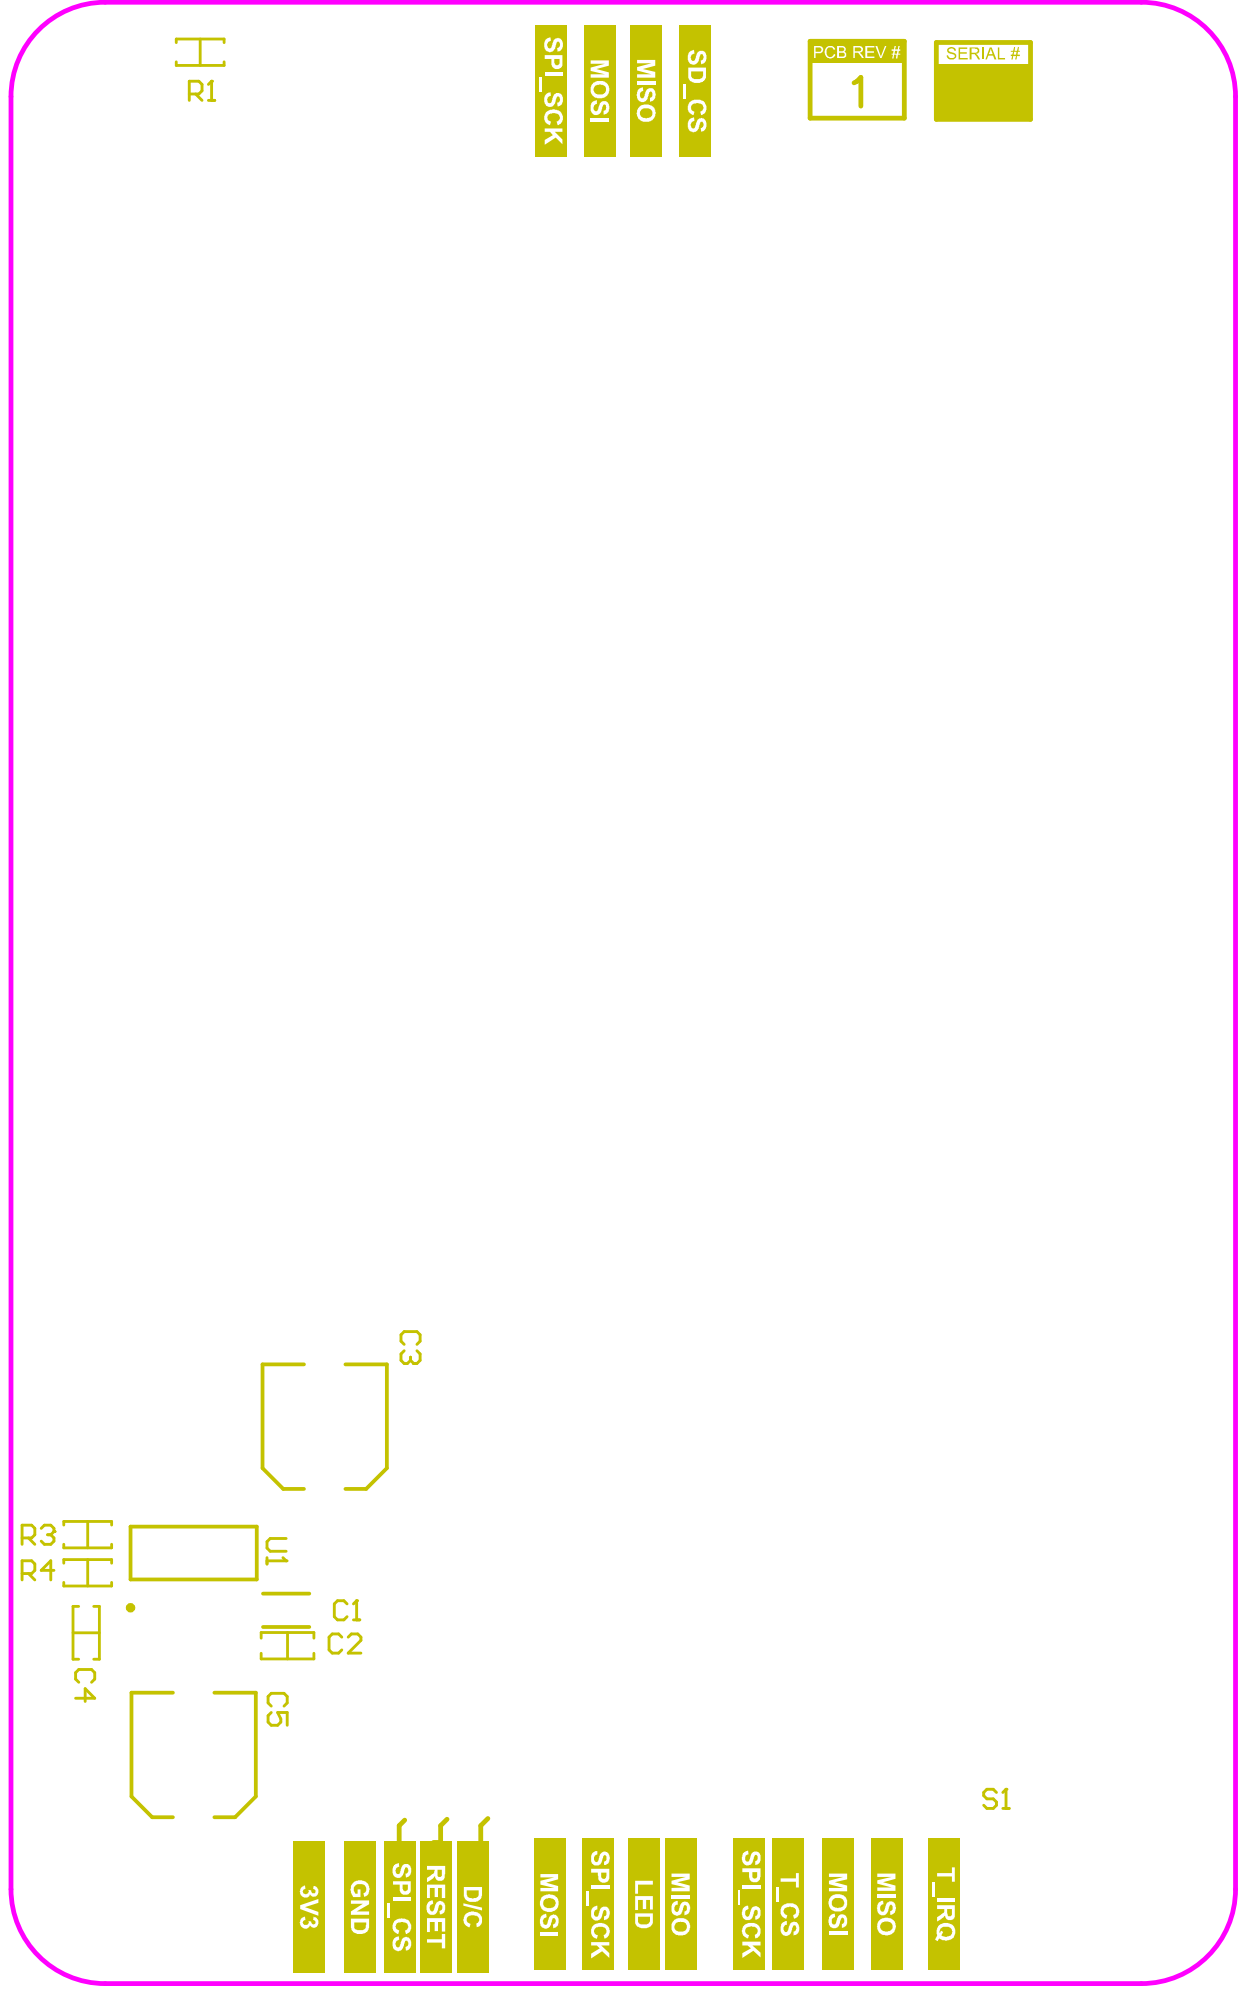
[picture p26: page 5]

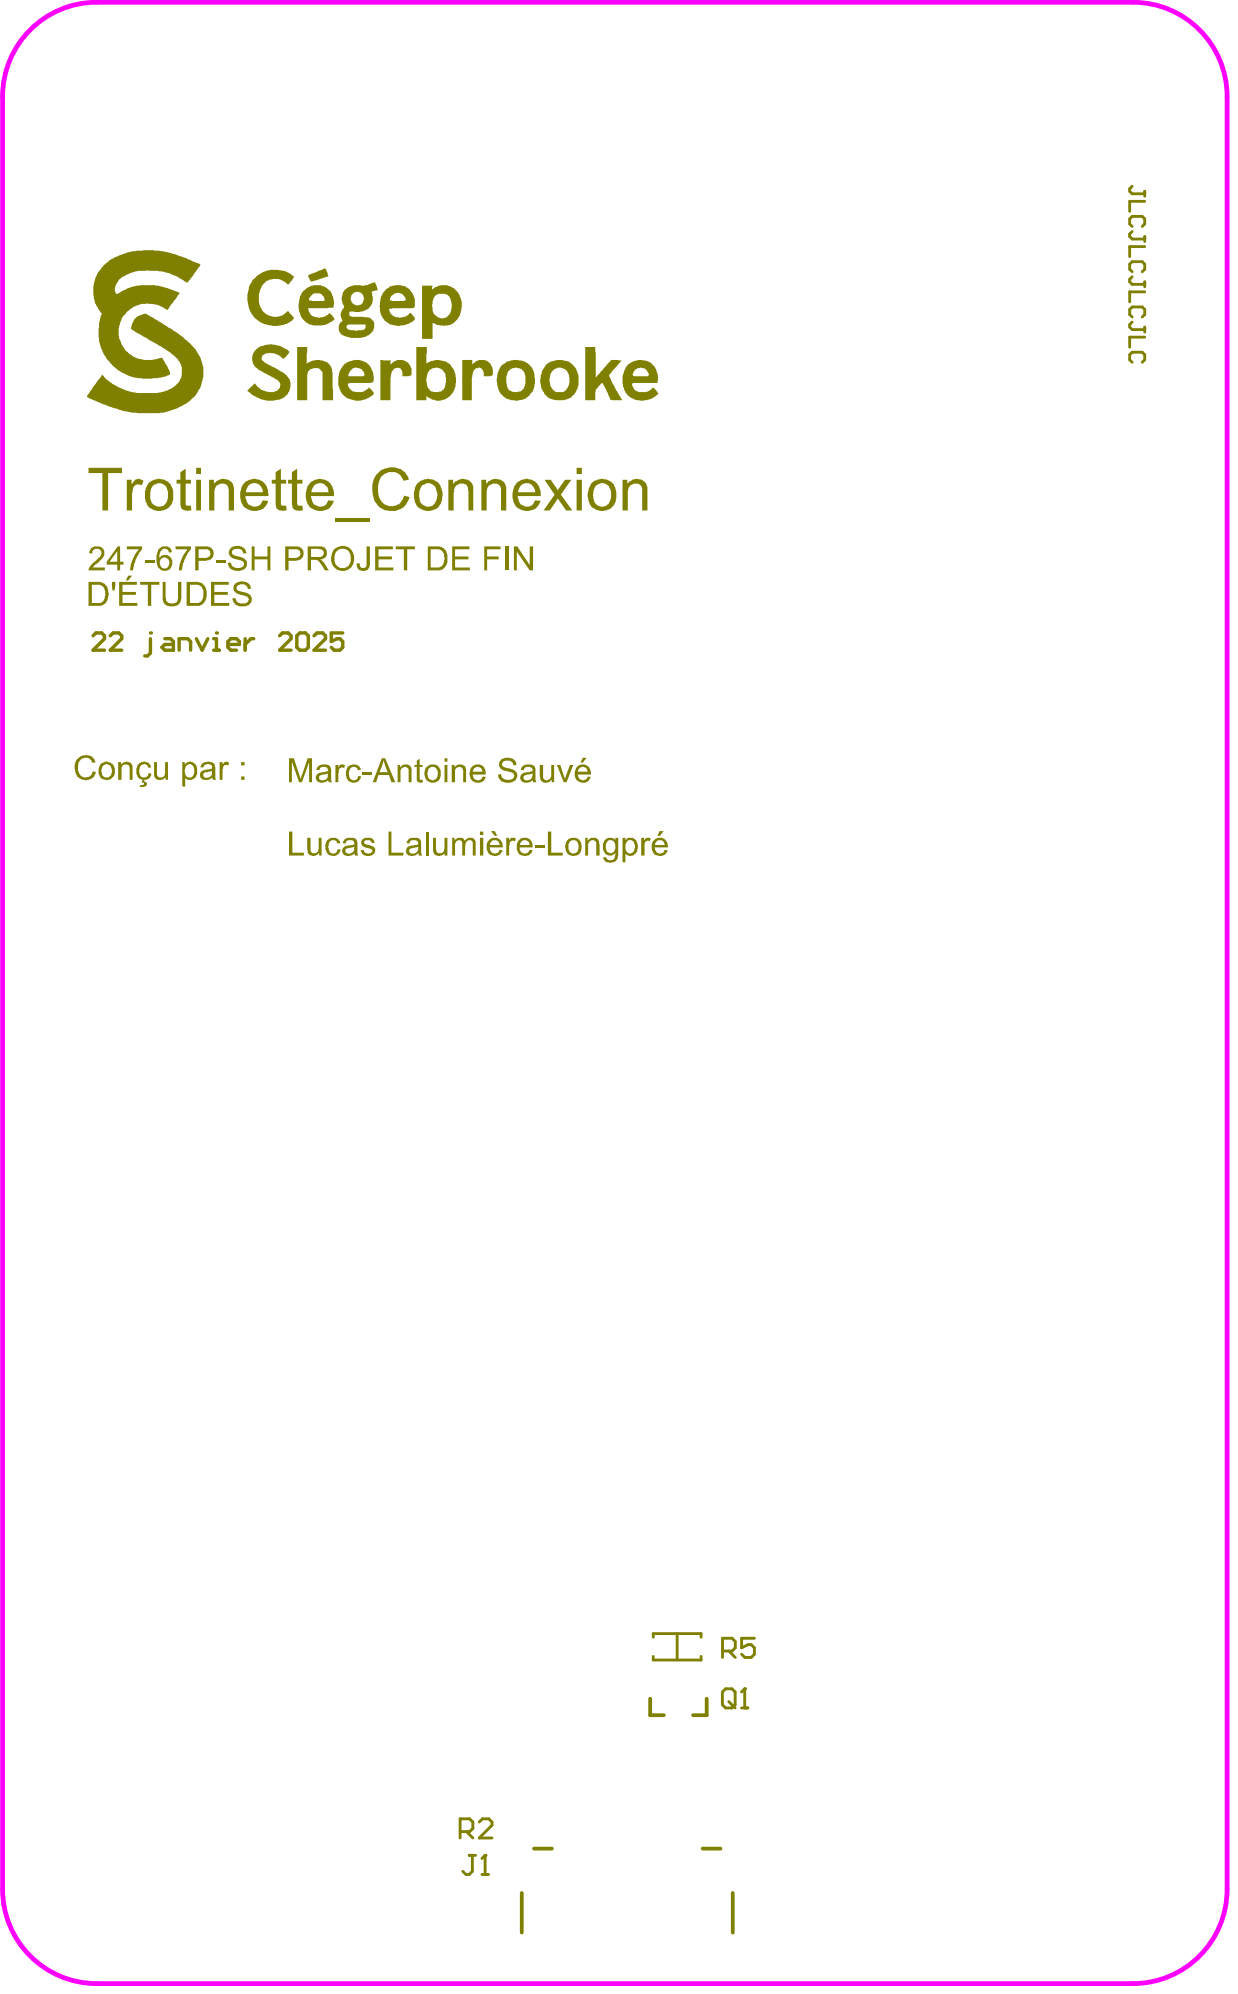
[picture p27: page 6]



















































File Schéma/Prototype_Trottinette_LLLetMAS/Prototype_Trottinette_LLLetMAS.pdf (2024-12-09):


247-575-SH Planification de Projet Revision

Titr
rotron Cours associé au projet


Nom de la feuille

Titredu projet
Prototype Accélérotron Cours associé au projet

247-575-SH Planification de Projet

Date 06/12/2024 | Feuille 2 de Concepteurs 3

Lucas Lalumière Longpré Marc-Antoine Sauvé


(SD = carte micro SD)

Titr
n Cours associé au projet

Date 06/12/2024 | F e uil l e 3 de Concepteurs 3

Lu c a s La l umi ère Lon g p r é Marc -A n toi n e S a u v é

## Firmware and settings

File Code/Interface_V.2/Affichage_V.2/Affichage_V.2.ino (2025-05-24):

/*
À faire :   
    Fait par : Marc-Antoine Sauvé et Lucas Lalumière Longpré

    Brief : Ce code permet de gérer l’interface graphique et la collecte de données d'une trottinette connectée avec un écran tactile. Il utilise la bibliothèque LVGL
    pour créer l’interface utilisateur, TFT_eSPI pour gérer l’écran, et des capteurs via I2C (accéléromètre). Il affiche la vitesse, la température, la tension de batterie
    et la commande d’accélération, en rafraîchissant dynamiquement ces données. L’écran peut afficher différentes pages (ex. : principale ou configuration) en fonction 
    de boutons tactiles. Le code lit aussi les données JSON via une liaison série pour mettre à jour l’affichage. Enfin, des modes débogage optionnels permettent de 
    suivre les touchers ou le pitch de l’appareil via le moniteur série.

    Date : 23 avril 2024
*/

#include <lvgl.h>             //libraries graphique
#include <TFT_eSPI.h>         //Librairie pour l'écran tactile
#include <ui.h>               // Fichier généré par EEZ studio
#include <SoftwareSerial.h>   //Permet l'utilisation de patte UART non programmé à 
#include <Wire.h>             //Lib I2C

#include "trottinetteAccelerometer.h"
#include "trottinetteData.h"
#include "trottinetteAffichage.h"

#define BYTE_PER_PIXEL (LV_COLOR_FORMAT_GET_SIZE(LV_COLOR_FORMAT_RGB565))

//---------------------------------Section DEBUG ---------------------------------//
#define modeDebug_JSON 0        //Print dans le moniteur série le JSON ou l'ereur si le JSON n'a pas été bien reçu
#define modeDebug_touch 0       //Print dans le moniteur série la valeur d'où on appuie sur l'écran
#define modeDebug_pitch 1       //Print dans le moniteur série 
#define modeDebug_temperature 0 //Print la température en degrés Celcius et Fahrenheit dans le moniteur série
#define mondeDubug_vitesse 0    //Print les valeur en kmh et en mp sur le moniteur série


#define avec_PCB_controleur 1   // 0 : permet de générer des données aléatoires pour l'affichage sans être connecter au PCB contrôleur
                                // 1 : permet de décoder le JSON envoyé par le PCB contrôleur
                              

//JSON
EspSoftwareSerial::UART jsonSerial; //Interface UART pour recevoir JSON

uint32_t draw_buf[DRAW_BUF_SIZE / 4];

const char vitesse_kmh [5] = "Km/h";
const char vitesse_mph [5]="mph";
const char* symbole_celsius = "°C";
const char* symbole_Fahrenheit = "°F";

//Touch screen
uint16_t calData[5] = { 243, 3618, 357, 3612, 4 };  //Valeurs de calibration de l'écran

//Vitesse
String vitesseString="";
int vitesseInt=0;
int vitesseInt_tamp=0;
char vitesseChar[4]="";
char vitesse_unite [5]="";

//Température
int temperatureInt = 0;
int temperatureInt_tamp =0;
char temperatureChar[4]="";
char symbole_temperature[4] = "°C";

//Charge de la Batterie
int tensionInt = 90;
char tensionChar[3]="";

//cmd (throttle)
int cmd = 0;
char cmdChar[3]="";

TFT_eSPI tft = TFT_eSPI(); //Déclare un objet pour l'écran tactile

//Elle redéfinit la manière dont les messages de log sont affichés en utilisant Serial.println sur un microcontrôleur (comme un ESP32 ou un Arduino).
#if LV_USE_LOG != 0
void my_print( lv_log_level_t level, const char * buf )
{
    LV_UNUSED(level);
    Serial.println(buf);
    Serial.flush();
}
#endif

// Utilise millis() d'Arduino comme source de tic 
static uint32_t my_tick(void)
{
    return millis();
}

// Si le PCB contrôleur n'envoie pas le JSON me le #define avec_PCB_controleur à 0
void generate_data(void)
{
  //Température  
  if (temperatureInt>=100)
  {
  temperatureInt = -20;
  }
  temperatureInt = temperatureInt +5;
  
  //Vitesse 
  if (vitesseInt>=50)
  {
  vitesseInt = 0;
  }
  vitesseInt= vitesseInt+4;

  //CMD 
  if (cmd>=100)
  {
    cmd = 0;
  }
  cmd = cmd +5;

  //Batterie
  if(tensionInt<=0)
  {
    tensionInt=100;
  }
  tensionInt= tensionInt-5;

/*
  //Print les données générées
  Serial.println("------Random data generated--------");
  Serial.print("Temperature : ");
  Serial.println(temperatureInt);

  Serial.print("Vitesse : ");
  Serial.println(vitesseInt);

  Serial.print("Tension : ");
  Serial.println(tensionInt);

  Serial.print("Cmd : ");
  Serial.println(cmd);

  Serial.println("-------------------------------");
  */
}

//Prend les données décodées du JSON envoyé par le PCB contrôleur
void refresh_data_affichage(void)
{
//Température
  temperatureInt=trottinette.drive.temperature;

//cmd (throttle)
  cmd=trottinette.ctrl.cmd;
    
//Tension de la batterie
  tensionInt=trottinette.drive.tension_total;
  tensionInt = tensionInt *100/36;


  if(trottinette.ctrl.speed_mode == "Lapin")// si le mode 1 = affiche le lapin sinon affiche la tortue
  {
    lv_obj_add_flag(objects.img_tortue, LV_OBJ_FLAG_HIDDEN);      // Pour cacher l'image tortue
    lv_obj_clear_flag(objects.img_lapin, LV_OBJ_FLAG_HIDDEN);    // Pour afficher l'image lapin

  }
  else if (trottinette.ctrl.speed_mode == "Tortue")
  {
      cmd = cmd*5;
      lv_obj_add_flag(objects.img_lapin, LV_OBJ_FLAG_HIDDEN);      // Pour cacher l'image lapin
      lv_obj_clear_flag(objects.img_tortue, LV_OBJ_FLAG_HIDDEN);    // Pour afficher l'image tortue
  }

//Vitesse
  vitesseString=trottinette.drive.vitesse;
}

//Permet le rapfraichissement des valeurs et couleur de l'affichage de la température sans avoir à décoder le JSON du PCB de contrôle
void temperature_refresh (int temperature)
{
  if (temperatureInt < LOW_TEMPERATURE)
  {
    lv_obj_set_style_text_color(objects.lb_temperature, lv_color_hex(color_low_temp), LV_PART_MAIN); // change la couleur
    lv_obj_set_style_border_color(objects.pnl_temperature, lv_color_hex(color_low_temp), LV_PART_MAIN);
    lv_obj_set_style_text_color(objects.lb_symbole_temperature, lv_color_hex(color_low_temp), LV_PART_MAIN);
  }
  else if (temperatureInt < HIGH_TEMPERATURE && temperatureInt>LOW_TEMPERATURE)
  {
    lv_obj_set_style_text_color(objects.lb_temperature, lv_color_hex(color_med_temp), LV_PART_MAIN); // change la couleur
    lv_obj_set_style_border_color(objects.pnl_temperature, lv_color_hex(color_med_temp), LV_PART_MAIN);
    lv_obj_set_style_text_color(objects.lb_symbole_temperature, lv_color_hex(color_med_temp), LV_PART_MAIN);
  }
  else if (temperatureInt > HIGH_TEMPERATURE)
  {
    lv_obj_set_style_text_color(objects.lb_temperature, lv_color_hex(color_high_temp), LV_PART_MAIN); // change la couleur
    lv_obj_set_style_border_color(objects.pnl_temperature, lv_color_hex(color_high_temp), LV_PART_MAIN);
    lv_obj_set_style_text_color(objects.lb_symbole_temperature, lv_color_hex(color_high_temp), LV_PART_MAIN);
  }
}

//Est l'action permettant à la page de configuration d'apparaitre sur l'écran lorsque le bouton de configuration est pesé
void event_handler_imgbtn_config(lv_event_t * e)
{
    lv_scr_load(objects.configuration);  // Affiche l'écran de configuration
}

//Est l'action permettant à la page de principale d'apparaitre sur l'écran lorsque le bouton retour est pesé
void event_handler_btn_retour_main(lv_event_t * e) 
{
    lv_scr_load(objects.main);  // Affiche l'écran de configuration
}

//Permet la gestion de la lecture en x et y de l'écran
void my_touchpad_read( lv_indev_t * indev, lv_indev_data_t * data )
  {
      //For example  ("my_..." functions needs to be implemented by you)
      uint16_t x, y;
      bool touched = tft.getTouch(&x, &y);
  
      if(!touched) {
          data->state = LV_INDEV_STATE_RELEASED;
      } else {
          data->state = LV_INDEV_STATE_PRESSED;
  
          data->point.x = x;
          data->point.y = y;
      }
}

//////////////////////à changer pour changer le fonctionnement des bouton dans configuration////////////////////////////////////////////////
//Permet de changer savoir
void event_handler_btn_vitesse(lv_event_t * e) {
    // Ce code sera exécuté lorsque le bouton est appuyé
    //Serial.println( "Bouton 'btn_vitesse' appuyé !"); //Au besoin pour un debug
}

void gestion_btn_conf()
{
  if(lv_obj_has_state(objects.btn_vitesse, LV_STATE_CHECKED))
    {
       strcpy(vitesse_unite, vitesse_mph);
    }
  else
    {
      strcpy(vitesse_unite, vitesse_kmh); 
    } 

  if (lv_obj_has_state(objects.btn_temperature, LV_STATE_CHECKED)) 
  {
    strcpy(symbole_temperature, symbole_Fahrenheit);
  } 
  else 
  {
    strcpy(symbole_temperature, symbole_celsius);
  }
}

void setup()
{
  if(modeDebug_touch||modeDebug_pitch || modeDebug_temperature|| mondeDubug_vitesse)
  {
    //Communication Serie
    Serial.begin(115200);
    Serial.println( "Communication serie active" );
  }
  
  jsonSerial.begin(115200, EspSoftwareSerial::SWSERIAL_8N1, RX_PIN, TX_PIN);  //Port pour recevoir objet JSON

  
  //I2C
    Wire.begin(SDA_PIN, SCL_PIN); //Initialise l'interface I2C
    initAccel();  //Initialise l'accelerometre

  //Permet d'allumer l'écran
    pinMode(LED_PIN, OUTPUT);
    digitalWrite(LED_PIN,LOW);

    pinMode(FALL_DETECT_PIN, OUTPUT);
    digitalWrite(FALL_DETECT_PIN, LOW);
    
    
  //Touch
    tft.setTouch(calData);  //Calibre l'écran avec les valeurs de calibration

  //LVGL
    lv_init();
    lv_tick_set_cb(my_tick);// Permet d'animer des objets, gérer les délais, animations, gestions tactiles. (Tout ce qui dépend du temps).
    lv_display_t * disp; //Créé un objet display pour que LVGL puisse avoir un espace de travail (sandbox)

    // register print function for debugging 
    #if LV_USE_LOG != 0
        lv_log_register_print_cb( my_print );
    #endif

    
  //TFT_eSPI
    #if LV_USE_TFT_ESPI
      //TFT_eSPI can be enabled lv_conf.h to initialize the display in a simple way
      disp = lv_tft_espi_create(TFT_HOR_RES, TFT_VER_RES, draw_buf, sizeof(draw_buf));
      lv_display_set_rotation(disp, TFT_ROTATION);
    #else
      //Else create a display yourself
      disp = lv_display_create(TFT_HOR_RES, TFT_VER_RES);
      lv_display_set_flush_cb(disp, my_disp_flush);
      lv_display_set_buffers(disp, draw_buf, NULL, sizeof(draw_buf), LV_DISPLAY_RENDER_MODE_PARTIAL);
    #endif
   
  lv_indev_t * indev = lv_indev_create();           //Create an input device
  lv_indev_set_type(indev, LV_INDEV_TYPE_POINTER);  //Touch pad is a pointer-like device
  lv_indev_set_read_cb(indev, my_touchpad_read);    //Set your driver function

  ui_init(); //Création des widgets (gestion du fichier ui)

  //Création des évènement des boutons
    lv_obj_add_event_cb(objects.imgbtn_config, event_handler_imgbtn_config, LV_EVENT_PRESSED, NULL);   //Assign an event callback
    lv_obj_add_event_cb(objects.btn_retour_main, event_handler_btn_retour_main, LV_EVENT_PRESSED, NULL);   //Assign an event callback
    lv_obj_add_event_cb(objects.btn_vitesse, event_handler_btn_vitesse, LV_EVENT_PRESSED, NULL);   //Assign an event callback

  // Paramétrage des widgets à mettre à jour avec notre code
    lv_arc_set_range(objects.arc_speed, arc_min, arc_max_kmh); // setup max et minimum de l'arc
    lv_scale_set_range(objects.scale_speed, arc_min, arc_max_kmh); // setup du scale visuel
    lv_bar_set_range(objects.bar_tension, bar_tension_min, bar_tension_max); // setup min et max de la bare de tension
    lv_bar_set_range(objects.bar_puissance, bar_cmd_min, bar_cmd_max); // setup min et max de la bare de tension

    Serial.println( "Setup done" ); // Ligne de test
}

void loop()
{
  if(modeDebug_touch)
  {
     //Test pour faire afficher la positionnement de touché de l'utilisateur 
    uint16_t t_x = 0, t_y = 0; //Variables pour storer les coordonnées du "touch"
    bool pressed = tft.getTouch(&t_x, &t_y);  //Vérifie si l'écran a été touché
    if (pressed == true)  //Si l'utilisateur touche l'écran
    { 
      Serial.print("x : ");
      Serial.print(t_x);
      Serial.print(", y : ");
      Serial.println(t_y);
    }
  }
  
  pitch = getPitch();//Calcule et retourne le pitch

  if(modeDebug_pitch)
  {
    //Affiche le pitch au moniteur série
      Serial.print("Pitch: ");
      Serial.println(pitch);
  }

  if (pitch >= 30 || pitch <= -30) 
  {  //Si la trottinette est penchée sur le côté
    digitalWrite(LED_PIN, HIGH);      //Éteind l'écran
    digitalWrite(FALL_DETECT_PIN, HIGH);
    Serial.print("Trottinette tombee (1)");
  }
  else 
  {
    digitalWrite(LED_PIN, LOW);       //Sinon, allume l'écran
    digitalWrite(FALL_DETECT_PIN, LOW);
    Serial.print("Trottinette droite (0)");
  }

  jsonString = jsonSerial.readStringUntil('\n');  //Lit le message recu jusqu'a \n
  jsonErrorMessage = jsonString;
  jsonError = deserializeJson(doc, jsonString);   //Décode l'objet

  if (!jsonError) //Si le JSON est décodé avec succès
  {         
    getData(doc);           //Enregistre les valeurs contenues dans l'objet json décodé
    if(modeDebug_JSON)
    { 
      printData(trottinette); //Affiche les données de la trottinette
    }
  }
  else {  //Si erreur de décodage
    if(modeDebug_JSON)
    { 
      Serial.println("JSON ERROR:");
      Serial.println(jsonErrorMessage);
    }
  }
  gestion_btn_conf();

  if (avec_PCB_controleur)//Avec ou sans PCB contrôleur
  {
    refresh_data_affichage(); //
  }
  else //Si on n'a pas le PCB controleur et qu'on veux générer des données 
  {
    generate_data();
  }


  
/////////////////////Mise à jour de l'écran///////////////////////////////

//Température
  if(modeDebug_temperature) // Permet de voir si la conversion de température est bonne 
  {
    Serial.println("Temperature Celsius : ");
    Serial.println(temperatureInt);
    temperatureInt_tamp = (temperatureInt*9/5)+32; // Formule pour passer de °C à °F
    Serial.println("Temperature Fahrenheit : ");
    Serial.println(temperatureInt_tamp);
  }
  if (strcmp(symbole_temperature, "°F") == 0)// Si la température doir être en °F
  {
    temperatureInt_tamp = (temperatureInt*9/5)+32; // Formule pour passer de °C à °F
    temperature_refresh(temperatureInt_tamp);
    itoa(temperatureInt_tamp, temperatureChar, 10);
  }
  else
  {
    temperature_refresh(temperatureInt);
    itoa(temperatureInt, temperatureChar, 10);
  }

  lv_label_set_text_fmt(objects.lb_symbole_temperature,symbole_temperature);
  lv_label_set_text_fmt(objects.lb_temperature,temperatureChar);

//Cmd (throttle)
  lv_bar_set_value(objects.bar_puissance, cmd, LV_ANIM_OFF); // à laisser avant la ligne dtostrf
  itoa(cmd, cmdChar, 10);
  lv_label_set_text_fmt(objects.lb_puissance,cmdChar);

//Tension de la batterie
  lv_bar_set_value(objects.bar_tension, tensionInt, LV_ANIM_OFF);  //// Change immédiatement à 50 (sans animation)
  itoa(tensionInt, tensionChar, 10);
  lv_label_set_text_fmt(objects.lb_tension,tensionChar);

//Vitesse   
  if(mondeDubug_vitesse)
  {
    Serial.print("Vitesse km/h : ");
    Serial.println(vitesseInt);
    vitesseInt_tamp = vitesseInt / 1.609; // calcul permettant de passer de km/h à mph
    Serial.print("Vitesse mph : ");
    Serial.println(vitesseInt_tamp);
  }
  if(avec_PCB_controleur)
  {
    vitesseInt =vitesseString.toInt();
  }
  if(strcmp(vitesse_unite, "mph") == 0)
  {
    vitesseInt_tamp = vitesseInt / 1.609; // calcul permettant de passer de km/h à mph
    itoa(vitesseInt_tamp, vitesseChar, 10);
    lv_arc_set_value(objects.arc_speed,vitesseInt_tamp);
    lv_arc_set_range(objects.arc_speed, arc_min, arc_max_mph); // setup max et minimum de l'arc
    lv_scale_set_range(objects.scale_speed, arc_min, arc_max_mph); // setup du scale visuel
  }
  else
  {
    itoa(vitesseInt, vitesseChar, 10);
    lv_arc_set_value(objects.arc_speed,vitesseInt);
    lv_arc_set_range(objects.arc_speed, arc_min, arc_max_kmh); // setup max et minimum de l'arc
    lv_scale_set_range(objects.scale_speed, arc_min, arc_max_kmh); // setup du scale visuel
  }
  lv_label_set_text_fmt(objects.lb_speed,vitesseChar);
  lv_label_set_text_fmt(objects.lb_unite_vitesse,vitesse_unite); /////////////////////////////////possibilité de ne pas le faire à chaque fois

//Gestion par lvgl et du UI
  lv_timer_handler(); // let the GUI do its work 
  ui_tick();
  //delay(10); // let this time pass 
}

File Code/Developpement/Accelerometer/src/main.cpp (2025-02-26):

/**
  @file   main.cpp, projet: Prototype affichage Trottinette électrique
  @author Lucas Lalumière Longpré
  @date   7 Octobre 2024
  @brief  Code pour le prototype du système d'affichage du
		      projet Trottinette électrique. Communique par I2C 
          avec un accéléromètre MPU-6050, à partir des valeurs
          X,Y,Z de l'accéléromètre, on calcule les valeurs de roulis
          et de tangage, ces valeurs sont utile pour la detection de 
          chute de la trottinette. Les deux valeurs sont affichées
          à l'écran et au terminal série. L'écran est tactile et affiche
          un message lorsqu'on appuie dessus. La DEL du MCU s'allume pour
          indiquer que la trottinette est tombée.

  Environnement:
      Développement: Visual Studio 2022
  Matériel: -MCU = ESP32-C3 DevkitC-02
            -Écran = ILI9341
            -Accéléromètre = MPU-6050
*/

#include <Arduino.h>
#include <Wire.h>
#include <SPI.h>
#include <math.h>
#include <TFT_eSPI.h>      //Librairie pour l'écran tactile

//Définition des paramètres pour l'écran
#define SCREEN_WIDTH 320
#define SCREEN_HEIGHT 240
uint16_t calData[5] = { 610, 2638, 592, 3103, 4 };  //Valeurs de calibration de l'écran

//Définition des pattes pour communication I2C
#define SDA_PIN 18  
#define SCL_PIN 19 

//Définition des paramètres pour l'accéléromètre
const uint8_t MPU=0x68; //Adresse de l'accéléromètre MPU 6050
int16_t AcX,AcY,AcZ;	//Valeurs X,Y,Z de l'accéléromètre
double g_pitch,g_roll;	//Variables de roulis (roll) et de tangage (pitch)

TFT_eSPI tft = TFT_eSPI(); //Déclare un objet pour l'écran tactile

void getAngle(int Vx,int Vy,int Vz);  //Fonction qui calcule le roulis et le tangage de l'accéléromètre

void setup() {
  Serial.begin(115200);

  tft.init();	//Initialise l'écran tactile
  tft.setRotation(0); //Écran en mode vertical
  //Vide l'écran et met la couleur de la police à noir
  tft.fillScreen(TFT_WHITE);
  tft.setTextColor(TFT_BLACK, TFT_WHITE);
  tft.setTouch(calData);  //Calibre l'écran avec les valeurs de calibration

  pinMode(LED_BUILTIN, OUTPUT);	//Initialise la DEL du MCU comme une sortie
  Wire.begin(SDA_PIN, SCL_PIN);	//Initialise la communication I2C
  Wire.beginTransmission(MPU);	//Commence la communication avec l'accéléromètre
  Wire.write(0x6B);   //Écrit au registre 0x6B PWR_MGMT1 (Power management)
  Wire.write(0);      //Met tous les bits de ce registre à 0, ce qui désactive le mode "sleep"
  Wire.endTransmission(true); //Arrête la transmission
}

void loop(){
  uint16_t t_x = 0, t_y = 0; //Variables pour storer les coordonnées du "touch"
  int AcXoff,AcYoff,AcZoff; //Variables d'offset pour X,Y,Z

  digitalWrite(LED_BUILTIN, LOW);	//Met la DEL à un niveau bas

  Wire.beginTransmission(MPU);  //Recommence la transmission avec l'accéléromètre
  Wire.write(0x3B); //Adresse le registre 0x3B (ACCEL_XOUT)
  Wire.endTransmission(false);  //Indique qu'on veut continuer la transmission
  Wire.requestFrom(MPU,(size_t)6,(bool)true);  //Fait une requête de données de 6 octets à l'accéléromètre en "repeated start"

  //Valeurs d'offset pour X,Y,Z
  AcXoff = -950;
  AcYoff = -300;
  AcZoff = 0;

  //Lit les données de l'accéléromètre
  AcX=(Wire.read()<<8|Wire.read()) + AcXoff;  //Combine les 8 bits LSB et les 8 bits MSB + le offset
  AcY=(Wire.read()<<8|Wire.read()) + AcYoff;
  AcZ=(Wire.read()<<8|Wire.read()) + AcZoff;

  //Calcule le roulis et tangage
  getAngle(AcX,AcY,AcZ);

  //Affiche les valeurs de roulis et de tangage au terminal série
  Serial.print("Angle: ");
  Serial.print("Pitch = "); Serial.print(g_pitch);
  Serial.print(" | Roll = "); Serial.println(g_roll);
  //Met la grosseur du tecte à 2, la couleur du texte est noire
  tft.setTextColor(TFT_BLACK);
  tft.setCursor(0,80);
  tft.setTextSize(2);
  //Affiche les valeurs de roulis et de tangage à l'écran
  tft.println("Angle: ");
  tft.print("Pitch = "); tft.println(g_pitch);
  tft.print("Roll = "); tft.println(g_roll);

  bool pressed = tft.getTouch(&t_x, &t_y);  //Vérifie si l'écran a été touché

  if (pressed == true) {  //Si l'utilisateur touche l'écran
    tft.setCursor(15,150);
    tft.print("SCREEN TOUCHED");  //Affiche un message à l'écran
  }

  if (g_pitch >= 30 || g_pitch <= -30)  { //Si le tangage est en haut de 30 ou plus bas que -30 (Trottinette tombée sur le côté)
    digitalWrite(LED_BUILTIN, HIGH);	//Allume la DEL du MCU
  }
  else if (g_roll >= 30 || g_roll <= -30) { //Si le roulis est en haut de 30 ou plus bas que -30 (Trottinette tombée vers l'avant ou vers l'arrière)
    digitalWrite(LED_BUILTIN, HIGH);
  }

  delay(500);
  tft.fillScreen(TFT_WHITE);  //Vide l'écran
}


/*Brief: Fonction pour convertir les valeurs x, y et z 
  provenant de l'accéléromètre en valeurs de roulis et 
  de tangage. Utile pour détecter si la trottinette est
  tombée sur le côté.
  Param: int Vx, Vy, Vz
  Return: Aucun
  */
void getAngle(int Vx,int Vy,int Vz) {
  double x = Vx;
  double y = Vy;
  double z = Vz;

  g_pitch = atan(x/sqrt((y*y) + (z*z)));  //Calcul du tangage en radian
  g_roll = atan(y/sqrt((x*x) + (z*z)));   //Calcul du roulis en radian
  //Convertie les valeurs en degré
  g_pitch = g_pitch * (180.0/3.14);
  g_roll = g_roll * (180.0/3.14);
}

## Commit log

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2024-11-18 Ajout du schéma de prototype
    Schéma électrique du prototype
    [ProtoAccélérotronLLLetMAS_Circuit.SchDoc, ProtoAccélérotronLLLetMAS_Title.SchDoc, ProtoAccélérotronLLLetMAS_overview.SchDoc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]
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2024-12-11 Correction Ben code final
    [main.cpp]
2025-01-22 Ajout du dossier schéma
    [AffichageTrottinette_LLLetMAS.PrjPcb, TEMPLATE_Circuit.SchDoc, TEMPLATE_Connectors.SchDoc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]
2025-01-22 déplacement du schéma prototype
    [ProtoAccélérotronLLLetMAS_Circuit.SchDoc, ProtoAccélérotronLLLetMAS_Title.SchDoc, ProtoAccélérotronLLLetMAS_overview.SchDoc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]
2025-01-22 Ajout schéma télémétrie
    [TEMPLATE_Circuit.SchDoc, TEMPLATE_Connectors.SchDoc, TEMPLATE_PCB_2L.PcbDoc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]
2025-01-22 Ajout de la lib de l'écran
    [ILI9341.SchLib, TEMPLATE_Circuit.SchDoc]
2025-01-22 Prep HDMI / ecran schema
    [TEMPLATE_PCB_2L.PcbDoc, Trottinette_Connexion_2L.PcbDoc, Trottinette_Connexion_PCB.SchDoc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]
2025-01-22 Début du schéma du PCB de télémétrie
    [TEMPLATE_Circuit.SchDoc]
2025-01-23 Schéma télémétrie
    [TEMPLATE_Circuit.SchDoc]
2025-01-27 Contiunation du schéma de télé
    [TEMPLATE_Circuit.SchDoc, trottinette_telemetrie.PrjPcb]
2025-01-27 Schema_elect_connexion et Layout
    [PcbLib1.PcbLib, Trottinette_Connexion.PrjPcb, Trottinette_Connexion_2L.PcbDoc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]
2025-01-27 Schéma télémétrie presque fini
    [TEMPLATE_Circuit.SchDoc]
2025-01-28 Télémétrie presque fini
    [TEMPLATE_Circuit.SchDoc, TEMPLATE_overview.SchDoc]
2025-01-28 Apres_schemaReview
    Ajout regulateur
    [PcbLib1.PcbLib, Trottinette_Connexion_2L.PcbDoc, Trottinette_Connexion_PCB.SchDoc]
2025-01-28 Ajout gitignore
    [TEMPLATE_Circuit.SchDoc, TEMPLATE_overview.SchDoc]
2025-01-28 Télémétrie reste pin headers
    [TEMPLATE_Circuit.SchDoc]
2025-01-29 Ajout LED pin
    [PcbLib1.PcbLib, Trottinette_Connexion_2L.PcbDoc, Trottinette_Connexion_PCB.SchDoc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]
2025-01-29 Ajout POR et Bootstrap
    [TEMPLATE_Circuit.SchDoc]
2025-01-30 Debut du PCB de connexion
    [Trottinette_Connexion_2L.PcbDoc, Trottinette_Connexion_PCB.SchDoc]
2025-01-30 Schéma télémétrie fini, reste paufinage
    [TEMPLATE_Circuit.SchDoc]
2025-02-03 Schéma télémétrie prêt pour revu
    [TEMPLATE_Circuit.SchDoc, TEMPLATE_Connectors.SchDoc, trottinette_telemetrie.PrjPcb]
2025-02-03 Layout_connexion
    ajout d'un mosfet pour le backlight
    [PcbLib1.PcbLib, Trottinette_Connexion.PrjPcb, Trottinette_Connexion_2L.PcbDoc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]
2025-02-04 Schéma télémétrie completé
    [TEMPLATE_Circuit.SchDoc, TEMPLATE_Connectors.SchDoc, Trottinette_Telemetrie_Circuit.SchDoc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]
2025-02-04 Modifs après revu schéma
    [Trottinette_Telemetrie_Circuit.SchDoc, Trottinette_Telemetrie_Connectors.SchDoc]
2025-02-04 Connexion_LAYOUT_v.1
    layout fini
    [Trottinette_Connexion_2L.PcbDoc, Trottinette_Connexion_PCB.SchDoc]
2025-02-05 Début du PCB de télémétrie
    [Trottinette_Telemetrie_Circuit.SchDoc, Trottinette_Telemetrie_PCB_2L.PcbDoc]
2025-02-05 Placement des composantes sur le PCB télé
    [Trottinette_Telemetrie_Circuit.SchDoc, Trottinette_Telemetrie_PCB_2L.PcbDoc]
2025-02-05 Plan de test PCB connexion v1
    [Trottinette_Connexion_2L.PcbDoc, plan_de_tests_PCB_Connexion.xlsx]
2025-02-06 Progrès sur PCB télé
    [Trottinette_Telemetrie_PCB_2L.PcbDoc]
2025-02-06 PCB review / changement non pas ajuster
    [PcbLib1.PcbLib, Trottinette_Connexion_2L.PcbDoc, Trottinette_Connexion_PCB.SchDoc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]
2025-02-10 PCB télémétrie nouveau layout de pieces
    [Trottinette_Telemetrie_Circuit.SchDoc, Trottinette_Telemetrie_Connectors.SchDoc, Trottinette_Telemetrie_PCB_2L.PcbDoc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]
2025-02-11 Routing télé fini
    [Trottinette_Telemetrie_Circuit.SchDoc, Trottinette_Telemetrie_Connectors.SchDoc, Trottinette_Telemetrie_PCB_2L.PcbDoc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]
2025-02-12 Ajout silkscreen télé
    [Trottinette_Telemetrie_PCB_2L.PcbDoc]
2025-02-12 Ajout du logo
    [Trottinette_Telemetrie_PCB_2L.PcbDoc]
2025-02-12 PCB télémétrie rev 1
    [Trottinette_Telemetrie_PCB_2L.PcbDoc]
2025-02-12 PCB Télémétrie Rev. 1
    [Trottinette_Telemetrie_PCB_2L.PcbDoc]
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2025-02-13 PCB télé après revu
    [Trottinette_Telemetrie_Circuit.SchDoc, Trottinette_Telemetrie_Connectors.SchDoc, Trottinette_Telemetrie_Title.SchDoc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]
2025-02-13 Deplacer HDMI
    [Trottinette_Connexion_2L.PcbDoc]
2025-02-18 PCB Connexion v1 outputJob
    [Trottinette_Connexion_2L.PcbDoc]
2025-02-18 outputjob v1 final
    [PcbLib1.PcbLib, Trottinette_Connexion.PrjPcb, Trottinette_Connexion_2L.PcbDoc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]
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2025-03-19 Ajout de notes pour REV 2
    [Trottinette_Telemetrie_Circuit.SchDoc, Trottinette_Telemetrie_Title.SchDoc, trottinette_telemetrie.PrjPcb]
2025-03-19 Notes pour rev 2
    [Trottinette_Telemetrie_Circuit.SchDoc]
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2025-04-07 Mise a jour
    Rev2 PCB et Code telemetrie
    [Trottinette_Telemetrie_Circuit.SchDoc, Trottinette_Telemetrie_Connectors.SchDoc, Trottinette_Telemetrie_Title.SchDoc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]
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2025-04-09 REV2 PCB près pour FAB
    [Trottinette_Telemetrie_Circuit.SchDoc, Trottinette_Telemetrie_Connectors.SchDoc, Trottinette_Telemetrie_Title.SchDoc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]
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2025-04-14 Fix de bugs variables
    [trottinetteAccelerometer.cpp, trottinetteData.cpp]
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
